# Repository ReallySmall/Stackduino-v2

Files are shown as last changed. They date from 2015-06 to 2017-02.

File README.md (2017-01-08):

Stackduino 2
==========
Please visit the project site for details: https://www.stackduino.net/boards/v2-2

Copyright 2017 Richard Iles

Permission is hereby granted, free of charge, to any person obtaining a copy of this software and associated documentation files (the "Software"), to deal in the Software without restriction, including without limitation the rights to use, copy, modify, merge, publish, distribute, sublicense, and/or sell copies of the Software, and to permit persons to whom the Software is furnished to do so, subject to the following conditions:

The above copyright notice and this permission notice shall be included in all copies or substantial portions of the Software.

THE SOFTWARE IS PROVIDED "AS IS", WITHOUT WARRANTY OF ANY KIND, EXPRESS OR IMPLIED, INCLUDING BUT NOT LIMITED TO THE WARRANTIES OF MERCHANTABILITY, FITNESS FOR A PARTICULAR PURPOSE AND NONINFRINGEMENT. IN NO EVENT SHALL THE AUTHORS OR COPYRIGHT HOLDERS BE LIABLE FOR ANY CLAIM, DAMAGES OR OTHER LIABILITY, WHETHER IN AN ACTION OF CONTRACT, TORT OR OTHERWISE, ARISING FROM, OUT OF OR IN CONNECTION WITH THE SOFTWARE OR THE USE OR OTHER DEALINGS IN THE SOFTWARE.

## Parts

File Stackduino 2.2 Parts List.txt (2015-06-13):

Partlist

Exported from Stackduino-SMD.sch at 13/06/2015 14:22:47

EAGLE Version 7.2.0 Copyright (c) 1988-2014 CadSoft

Assembly variant: 

Part          Value                   Device              Package            Library                  Sheet

A4988_CARRIER A4988BREAKOUT           A4988BREAKOUT       A4988BREAKOUT      RepRapjr                 1
ATMEGA328P    ATMEGA328P              ATMEGA328_SMT       TQFP32-08          SparkFun-DigitalIC       1
BATT_IN       JST-PH_3-PIN_HEADER     JST-PH_3-PIN_HEADER JST_B3B-PH_HEADER  SRG                      1
C1            22pF                    C                   C0805              eagle-ltspice            1
C2            0.1uF                   C                   C0805              eagle-ltspice            1
C3            0.1uF                   C                   C0805              eagle-ltspice            1
C4            10nF                    C                   C0805              eagle-ltspice            1
C5            0.1uF                   C                   C0805              eagle-ltspice            1
C6            22pF                    C                   C0805              eagle-ltspice            1
C7            0.1uF                   C                   C0805              eagle-ltspice            1
C8            100uF                   CAP_POLD            PANASONIC_D        SparkFun-Passives        1
C9            100uF                   CAP_POLD            PANASONIC_D        SparkFun-Passives        1
C10           100uF                   CAP_POLD            PANASONIC_D        SparkFun-Passives        1
C11           0.1uF                   C                   C0805              eagle-ltspice            1
C12           0.1uF                   C                   C0805              eagle-ltspice            1
C13           100nF                   C                   C0805              eagle-ltspice            1
C14           22uF                    C                   C0805              eagle-ltspice            1
C15           10nF                    C                   C0805              eagle-ltspice            1
D1            20v 1A                  MBRA140             SMA-DIODE          SparkFun-DiscreteSemi    1
D2            20v 1A                  MBRA140             SMA-DIODE          SparkFun-DiscreteSemi    1
DB15          DB15                    DB15                DB15               SparkFun-Connectors      1
DC_SOCKET     2.1MMJACKTHM            2.1MMJACKTHM        PJ-102A            adafruit                 1
FT232RL       FT232RLSSOP             FT232RLSSOP         SSOP28DB           SparkFun-DigitalIC       1
H1            MOUNT-PAD-ROUND2.8      MOUNT-PAD-ROUND2.8  2,8-PAD            holes                    1
H2            MOUNT-PAD-ROUND2.8      MOUNT-PAD-ROUND2.8  2,8-PAD            holes                    1
H3            MOUNT-PAD-ROUND2.8      MOUNT-PAD-ROUND2.8  2,8-PAD            holes                    1
H4            MOUNT-PAD-ROUND2.8      MOUNT-PAD-ROUND2.8  2,8-PAD            holes                    1
H_1           B4B-ZR                  B4B-ZR              B4B-ZR             jst-connectors           1
H_2           B4B-ZR                  B4B-ZR              B4B-ZR             jst-connectors           1
H_3           B3B-ZR                  B3B-ZR              B3B-ZR             jst-connectors           1
H_4           B5B-ZR                  B5B-ZR              B5B-ZR             jst-connectors           1
H_5           B10B-ZR                 B10B-ZR             B10B-ZR            jst-connectors           1
H_6           B2B-ZR                  B2B-ZR              B2B-ZR             jst-connectors           1
H_7           B2B-ZR                  B2B-ZR              B2B-ZR             jst-connectors           1
H_8           B2B-ZR                  B2B-ZR              B2B-ZR             jst-connectors           1
J1            JUMPER                  R                   R0805              eagle-ltspice            1
J2                                    PINHD-1X2           1X02               pinhead                  1
L1            33uH - Coilcraft DO3316 DO3316P             DO3316P            inductor-coilcraft       1
LM2675-3.3    LM2675M                 LM2675M             SO08               v-reg-3                  1
LTC2950       LTC2950CTS8-1TRPBF      LTC2950CTS8-1TRPBF  SOT65P280X100-8N   LTC_By_element14_Batch_1 1
LTC4412       LTC4412ES6PBF           LTC4412ES6PBF       SOT95P280X100-6N   LTC_By_element14_Batch_1 1
MCP23017      MCP23017SS              MCP23017SS          SSOP28             adafruit                 1
MICROSD       CON_MICROSDHINGED       CON_MICROSDHINGED   CON_MICROSD_HINGED dp_devices               1
MN1           BSS123                  BSS123              SOT23              transistor-small-signal  1
MP1           FDN306P                 FDN360P             SUPER-SOT3         transistor-power         1
MP2           FDN306P                 FDN360P             SUPER-SOT3         transistor-power         1
MP3           FDN340P                 FDN360P             SUPER-SOT3         transistor-power         1
OPT1          AVAGO HCPL-181-00BE     LTV816S             SMD4               optocoupler              1
OPT2          AVAGO HCPL-181-00BE     LTV816S             SMD4               optocoupler              1
QF1           8Mhz                    CRYSTALHC49U-V      HC49U-V            crystal                  1
R1            220 Ohm                 R                   R0805              eagle-ltspice            1
R2            220 Ohm                 R                   R0805              eagle-ltspice            1
R3            100K                    R                   R0805              eagle-ltspice            1
R4            2.7K                    R                   R0805              eagle-ltspice            1
R5            10K                     R                   R0805              eagle-ltspice            1
R6            4.7K                    R                   R0805              eagle-ltspice            1
R7            4.7K                    R                   R0805              eagle-ltspice            1
R8            10K                     R                   R0805              eagle-ltspice            1
R9            10K                     R                   R0805              eagle-ltspice            1
R10           10K                     R                   R0805              eagle-ltspice            1
R11           10K                     R                   R0805              eagle-ltspice            1
R12           100K                    R                   R0805              eagle-ltspice            1
R13           100K                    R                   R0805              eagle-ltspice            1
R14           100K                    R                   R0805              eagle-ltspice            1
R15           600K                    R                   R0805              eagle-ltspice            1
USB           USBSMD                  USBSMD              USB-MINIB          SparkFun-Connectors      1

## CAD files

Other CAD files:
Sketchup/Stackduino-2.2-Sketchup.skp

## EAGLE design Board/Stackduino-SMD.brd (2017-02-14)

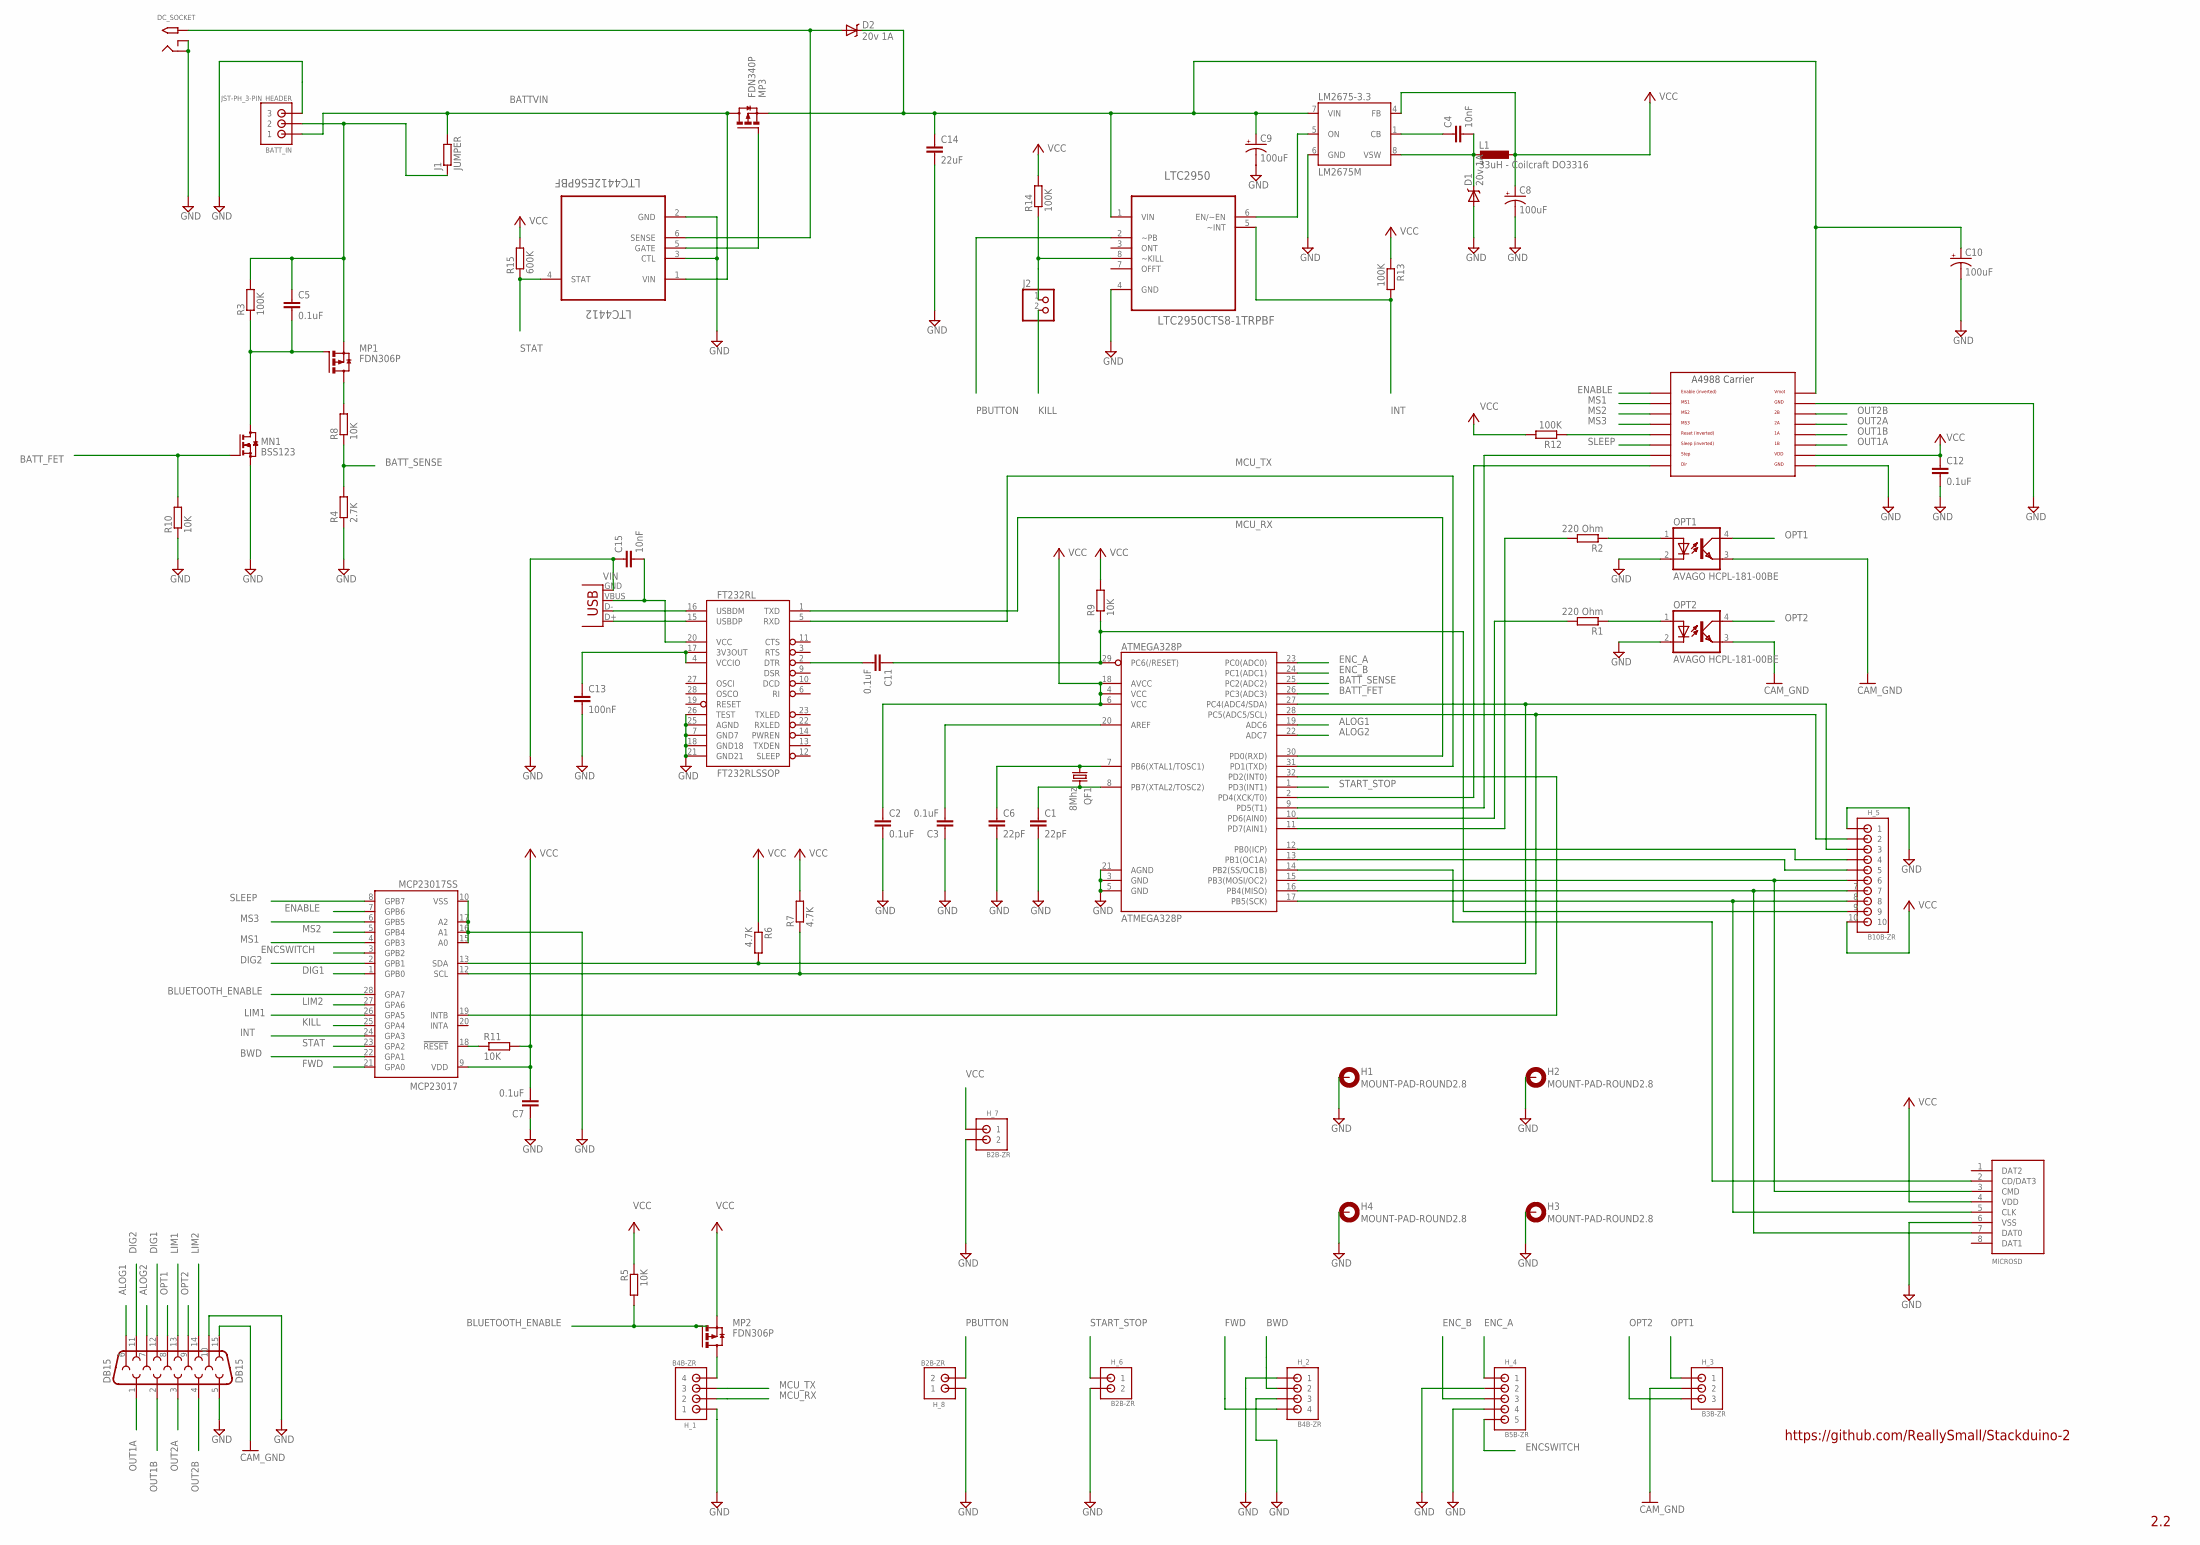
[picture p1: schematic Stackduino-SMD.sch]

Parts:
A4988_CARRIER: A4988BREAKOUT
ATMEGA328P: ATMEGA328P; TQFP32-08
BATT_IN: JST-PH_3-PIN_HEADER; JST_B3B-PH_HEADER
C1, C6: 22pF; C0805
C2, C3, C5, C7, C11, C12: 0.1uF; C0805
C4, C15: 10nF; C0805
C8, C9, C10: 100uF; PANASONIC_D
C13: 100nF; C0805
C14: 22uF; C0805
D1, D2: 20v 1A; SMA-DIODE
DB15: DB15
DC_SOCKET: 2.1MMJACKTHM; PJ-102A
FT232RL: FT232RLSSOP; SSOP28DB
H1, H2, H3, H4: MOUNT-PAD-ROUND2.8; 2,8-PAD
H_1, H_2: B4B-ZR
H_3: B3B-ZR
H_4: B5B-ZR
H_5: B10B-ZR
H_6, H_7, H_8: B2B-ZR
J1: JUMPER; R0805
J2: PINHD-1X2; 1X02
L1: 33uH - Coilcraft DO3316; DO3316P
LM2675-3.3: LM2675M; SO08
LTC2950: LTC2950CTS8-1TRPBF; SOT65P280X100-8N
LTC4412: LTC4412ES6PBF; SOT95P280X100-6N
MCP23017: MCP23017SS; SSOP28
MICROSD: CON_MICROSDHINGED; CON_MICROSD_HINGED
MN1: BSS123; SOT23
MP1, MP2: FDN306P; SUPER-SOT3
MP3: FDN340P; SUPER-SOT3
OPT1, OPT2: AVAGO HCPL-181-00BE; SMD4
QF1: 8Mhz; HC49U-V
R1, R2: 220 Ohm; R0805
R3, R12, R13, R14: 100K; R0805
R4: 2.7K; R0805
R5, R8, R9, R10, R11: 10K; R0805
R6, R7: 4.7K; R0805
R15: 600K; R0805
USB: USBSMD; USB-MINIB

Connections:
3V3_SET: C13.1, FT232RL.4 (VCCIO), FT232RL.17 (3V3OUT)
A4988_RESET: A4988_CARRIER.RST, R12.1
ALOG1: ATMEGA328P.19 (ADC6), DB15.6
ALOG2: ATMEGA328P.22 (ADC7), DB15.7
BATTVIN: BATT_IN.P1 (1), J1.2, LTC4412.1 (VIN), MP3.3 (D)
BATT_FET: ATMEGA328P.26 (PC3(ADC3)), MN1.1 (G), R10.2
BATT_SENSE: ATMEGA328P.25 (PC2(ADC2)), R4.2, R8.1
BATT_SENSE_UPSTREAM: MP1.3 (D), R8.2
BATT_VOLT: BATT_IN.P2 (2), C5.1, J1.1, MP1.2 (S), R3.2
BATT_VOLT_ENABLE: C5.2, MN1.3 (D), MP1.1 (G), R3.1
BLUETOOTH_ENABLE: MCP23017.28 (GPA7), MP2.1 (G), R5.2
BWD: H_2.2, MCP23017.22 (GPA1)
CAM_GND: DB15.15, H_3.2, OPT1.3 (EMIT), OPT2.3 (EMIT)
DIG1: DB15.12, MCP23017.1 (GPB0)
DIG2: DB15.11, MCP23017.2 (GPB1)
DIR: A4988_CARRIER.DIR, ATMEGA328P.2 (PD4(XCK/T0))
ENABLE: A4988_CARRIER.EN, MCP23017.7 (GPB6)
ENCSWITCH: H_4.5, MCP23017.3 (GPB2)
ENC_A: ATMEGA328P.23 (PC0(ADC0)), H_4.1
ENC_B: ATMEGA328P.24 (PC1(ADC1)), H_4.3
FWD: H_2.4, MCP23017.21 (GPA0)
GATE: LTC4412.5 (GATE), MP3.1 (G)
GND: A4988_CARRIER.GND, A4988_CARRIER.GND@0 (GND), ATMEGA328P.3 (GND), ATMEGA328P.5 (GND), ATMEGA328P.21 (AGND), BATT_IN.P3 (3), C1.2, C2.2, C3.1, C6.2, C7.1, C8.-, C9.-, C10.-, C12.2, C13.2, C14.2, C15.1, D1.A, DB15.5, DB15.10, DC_SOCKET.RING, DC_SOCKET.RING_SW, FT232RL.7 (GND7), FT232RL.18 (GND18), FT232RL.21 (GND21), FT232RL.25 (AGND), FT232RL.26 (TEST), H1.B2,8, H2.B2,8, H3.B2,8, H4.B2,8, H_1.1, H_2.1, H_2.3, H_4.2, H_4.4, H_5.1, H_6.2, H_7.2, H_8.1, LM2675-3.3.6 (GND), LTC2950.4 (GND), LTC4412.2 (GND), LTC4412.3 (CTL), MCP23017.10 (VSS), MCP23017.15 (A0), MCP23017.16 (A1), MCP23017.17 (A2), MICROSD.6 (VSS), MN1.2 (S), OPT1.2 (C), OPT2.2 (C), R4.1, R10.1, USB.GND
I2C_SCL: ATMEGA328P.28 (PC5(ADC5/SCL)), H_5.2, MCP23017.12 (SCL), R7.1
I2C_SDA: ATMEGA328P.27 (PC4(ADC4/SDA)), H_5.3, MCP23017.13 (SDA), R6.2
INT: LTC2950.5 (~INT), MCP23017.24 (GPA3), R13.2
KILL: J2.2, MCP23017.25 (GPA4)
KILL_2: J2.1, LTC2950.8 (~KILL), R14.1
LIM1: DB15.13, MCP23017.26 (GPA5)
LIM2: DB15.14, MCP23017.27 (GPA6)
LM2675_CB: C4.1, LM2675-3.3.1 (CB)
LM2675_ENABLE: LM2675-3.3.5 (ON), LTC2950.6 (EN/~EN)
LM2675_OUT: C4.2, D1.C, L1.1, LM2675-3.3.8 (VSW)
MCP_INT: ATMEGA328P.32 (PD2(INT0)), MCP23017.19 (INTB)
MCP_RESET: MCP23017.18 (!RESET), R11.1
MCU_RX: ATMEGA328P.30 (PD0(RXD)), FT232RL.1 (TXD), H_1.2
MCU_TX: ATMEGA328P.31 (PD1(TXD)), FT232RL.5 (RXD), H_1.3
MISO: ATMEGA328P.16 (PB4(MISO)), H_5.7, MICROSD.7 (DAT0)
MOSI: ATMEGA328P.15 (PB3(MOSI/OC2)), H_5.6, MICROSD.3 (CMD)
MS1: A4988_CARRIER.MS1, MCP23017.4 (GPB3)
MS2: A4988_CARRIER.MS2, MCP23017.5 (GPB4)
MS3: A4988_CARRIER.MS3, MCP23017.6 (GPB5)
unnamed: C11.2, FT232RL.2 (DTR)
unnamed: FT232RL.16 (USBDM), USB.D-
unnamed: FT232RL.15 (USBDP), USB.D+
unnamed: ATMEGA328P.20 (AREF), C3.2
unnamed: H_1.4, MP2.3 (D)
unnamed: C15.2, FT232RL.20 (VCC), USB.VBUS
OPT1: DB15.8, H_3.1, OPT1.4 (COL)
OPT1_IN: OPT1.1 (A), R2.1
OPT1_MCU: ATMEGA328P.11 (PD7(AIN1)), R2.2
OPT2: DB15.9, H_3.3, OPT2.4 (COL)
OPT2_IN: OPT2.1 (A), R1.1
OPT2_MCU: ATMEGA328P.10 (PD6(AIN0)), R1.2
OUT1A: A4988_CARRIER.1B, DB15.1
OUT1B: A4988_CARRIER.1A, DB15.2
OUT2A: A4988_CARRIER.2A, DB15.3
OUT2B: A4988_CARRIER.2B, DB15.4
PBUTTON: H_8.2, LTC2950.2 (~PB)
RESET: ATMEGA328P.29 (PC6(/RESET)), C11.1, H_5.9, R9.1
SCK: ATMEGA328P.17 (PB5(SCK)), H_5.8, MICROSD.5 (CLK)
SLEEP: A4988_CARRIER.SLP (SLEEP), MCP23017.8 (GPB7)
SS_1: ATMEGA328P.14 (PB2(SS/OC1B)), MICROSD.2 (CD/DAT3)
SS_2: ATMEGA328P.13 (PB1(OC1A)), H_5.5
SS_3: ATMEGA328P.12 (PB0(ICP)), H_5.4
START_STOP: ATMEGA328P.1 (PD3(INT1)), H_6.1
STAT: LTC4412.4 (STAT), MCP23017.23 (GPA2), R15.1
STEP: A4988_CARRIER.STEP, ATMEGA328P.9 (PD5(T1))
V+: A4988_CARRIER.VMOT, C9.+, C10.+, C14.1, D2.C, LM2675-3.3.7 (VIN), LTC2950.1 (VIN), MP3.2 (S)
VCC: A4988_CARRIER.VDD, ATMEGA328P.4 (VCC), ATMEGA328P.6 (VCC), ATMEGA328P.18 (AVCC), C2.1, C7.2, C8.+, C12.1, H_5.10, H_7.1, L1.2, LM2675-3.3.4 (FB), MCP23017.9 (VDD), MICROSD.4 (VDD), MP2.2 (S), R5.1, R6.1, R7.2, R9.2, R11.2, R12.2, R13.1, R14.2, R15.2
VIN: D2.A, DC_SOCKET.TIP, LTC4412.6 (SENSE)
XTAL1: ATMEGA328P.7 (PB6(XTAL1/TOSC1)), C6.1, QF1.1
XTAL2: ATMEGA328P.8 (PB7(XTAL2/TOSC2)), C1.1, QF1.2

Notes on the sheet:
https://github.com/ReallySmall/Stackduino-2
2.2

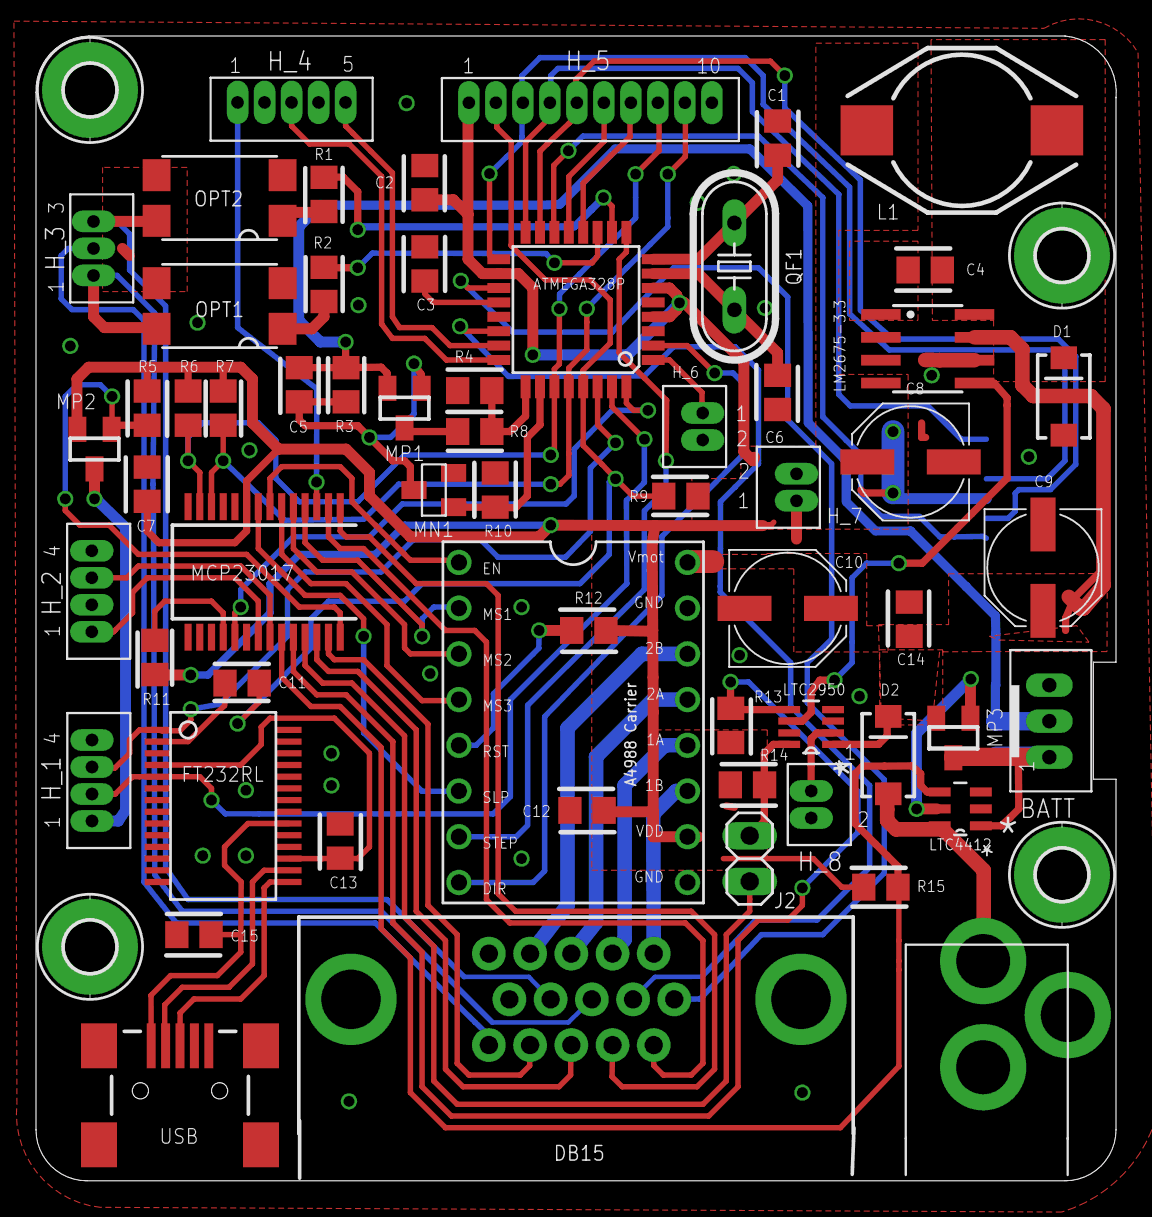
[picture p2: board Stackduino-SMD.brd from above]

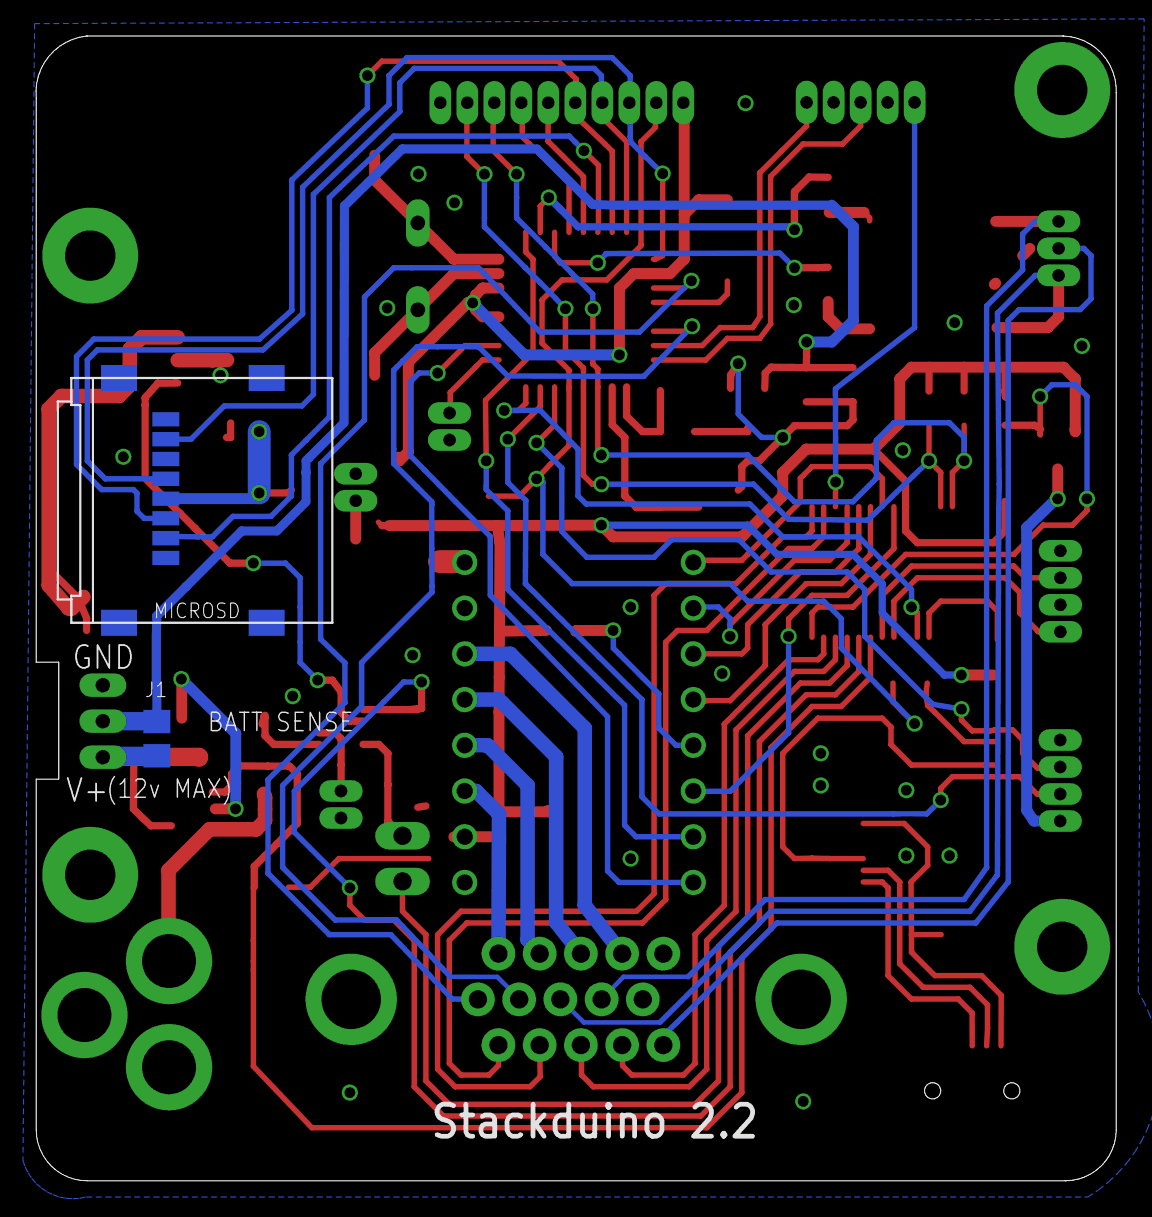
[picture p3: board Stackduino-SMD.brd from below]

Board: 2 copper layers, 60.0 x 63.6 mm, 66 parts (2 on the bottom side), 73 nets.

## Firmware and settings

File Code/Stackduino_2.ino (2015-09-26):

//////////////////////////////////////////////////////////////////////////////////////////////////////////
//  STACKDUINO 2 (BETA)                                                                                 //
//                                                                                                      //
//  https://github.com/ReallySmall/Stackduino-2                                                         //
//                                                                                                      //
//  An Arduino compatible Focus Stacking Controller optimised for mobile use                            //
//  Richard Iles 2014                                                                                   //
//                                                                                                      //
//  Written for use with the Digole 128 x 64 OLED module using default font (4 rows of 16 chars)        //
//  To support other fonts or screens, some recoding will be required                                   //
////////////////////////////////////////////////////////////////////////////////////////////////////////*/



/* DEFINES AND DEPENDENCIES */
#define _Digole_Serial_I2C_ // OLED screen configured with solder jumper to run in I2C mode
#define OLED_ROWS 4 // OLED text rows
#define OLED_COLS 16 // OLED text columns
#define ENC_A A0 // Rotary encoder
#define ENC_B A1 // Rotary encoder
#define ENC_PORT PINC // Rotary encoder
#define settings_elements 4 // Number of properties in each settings

#include "DigoleSerial.h" // https://github.com/chouckz/HVACX10Arduino/blob/master/1.0.1_libraries/DigoleSerial/DigoleSerial.h
#include "Wire.h" //
#include "Adafruit_MCP23017.h" //
#include "SPI.h"
#include "SD.h"
#include "avr/pgmspace.h"



/* CREATE REQUIRED OBJECTS */
Adafruit_MCP23017 mcp; // 16 pin IO port expander
DigoleSerialDisp screen(&Wire, '\x27'); // Digole OLED in i2c mode

typedef struct { // A struct type for storing char arrays
  char title [OLED_COLS + 1];
} stringConstants;

const stringConstants settings_titles[] PROGMEM = { // A struct of char arrays stored in Flash
  {"Stackduino v2.2"},
  {"Slice size"},
  {"Slices"},
  {"Pause for"},
  {"Mirror lockup"},
  {"Bracketing"},
  {"Return to home"},
  {"Units"},
  {"Motor speed"},
  {"Microsteps"},
  {"Bluetooth"}
};

char uom_chars[3] = {'u', 'm', 'c'};

struct Settings { // A struct type for storing settings

  int value; // The setting value
  byte lower; // The lowest value the setting may have
  int upper; // The highest value the setting may have
  byte multiplier; // Any multiplier to apply when the setting is incremented

} settings[] = { // A struct of user menu settings
  {}, // The home screen - not actually used by any functions at the moment, but the placeholder array must exist to maintain the correct indexing
  {10, 10, 500, 1}, // "Slice size"
  {10, 10, 500, 10}, // "Number of slices"
  {5, 1, 60, 1}, // "Pause time"
  {0, 0, 1, 1}, // "Mirror lockup"
  {1, 1, 10, 1}, // "Bracketing"
  {0, 0, 1, 1}, // "Return to start"
  {0, 0, 2, 1}, // "Unit of measure"
  {2, 1, 8, 1}, // "Stepper speed"
  {4, 0, 4, 1}, // "Microstepping"
  {0, 0, 1, 1} // "Bluetooth"
};

byte settings_count = sizeof(settings) / sizeof(Settings); // The number of settings
char char_buffer[OLED_COLS + 1]; // make sure this is large enough for the largest string it must hold



/* SET UP REMAINING ATMEGA PINS */
const byte mcp_int = 2; // Incoming MCP23017 interrupts
const byte btn_main = 3;  // Main start/ stop stack button
const byte step_dir = 4; // Direction pin on A4988 stepper driver
const byte do_step = 5; // Step pin on A4988 stepper driver
const byte cam_focus = 6; // Camera autofocus signal
const byte cam_shutter = 7; // Camera shutter signal
const byte sd_ss = 10; // SPI slave select for SD card slot
const byte batt_sense = A2; // Battery voltage sampling
const byte batt_fet = 17; // Connect/ disconnect battery voltage sampling line
const byte alog_1 = A6; // Analogue pin (supports analogueRead() only) broken out through DB15 - currently unused
const byte alog_2 = A7; // Analogue pin (supports analogueRead() only) broken out through DB15 - currently unused



/*  SET UP MCP23017 PINS */
const byte step_bwd = 0; // For manual stage positioning
const byte step_fwd = 1; // For manual stage positioning
const byte pwr_stat = 2; // LTC4412 stat pin - indicates whether controller is currently powered by wall adapter or battery
const byte switch_off_flag = 3; // LTC2950 int pin - signals to the controller that it is about to be switched off
const byte switch_off = 4; // LTC2950 kill pin - disables 3.3v regulator and switches off controller
const byte limit_switch_front = 5; // Limit switch to stop stepper motor if end of travel is reached
const byte limit_switch_back = 6; // Limit switch to stop stepper motor if end of travel is reached
const byte bluetooth_pwr_toggle = 7; // Toggles power to bluetooth breakout board header
const byte connected_hardware = 8; // Digital pin broken out through DB15 - currently unused
const byte dig_1 = 9;// Digital pin broken out through DB15 - currently unused
const byte btn_rotary = 10; // Select/ unselect menu item button
const byte ms1 = 11; // Toggles A4988 stepper driver MS1 pin to control degree of microstepping
const byte ms2 = 12; // Toggles A4988 stepper driver MS2 pin to control degree of microstepping
const byte ms3 = 13; // Toggles A4988 stepper driver MS3 pin to control degree of microstepping
const byte step_enable = 14; // Disable/enables A4988 stepper driver to conserve power
const byte step_sleep = 15; // Sleep/wake A4988 stepper driver to conserve power



/* SETTINGS */
const int uom_multipliers[] = {1, 1000, 10000}; // Multipliers for active unit of measure (mn, mm or cm)
const byte micro_stepping[2][5][3] = {{{1},       {2},       {4},       {8},       {16}}, // Degrees of microstepping the A4988 stepper driver can use
  {{0, 0, 0}, {1, 0, 0}, {0, 1, 0}, {1, 1, 0}, {1, 1, 1}}
}; // HIGH/ LOW combinations to set A4988 MSx pins at

float active_hardware_calibration_setting;

volatile boolean start_stack = false; // False when in the menu, true when stacking
volatile boolean traverse_menus = true; // True when scrolling through menus, false when changing a menu item's value
volatile boolean mcp_int_fired = false; // True whenever a pin on the mcp23017 with a listener went low
volatile byte btn_reading; // The current reading from the button
volatile byte btn_previous = LOW; // The previous reading from the button
volatile long btn_time = 0; // The last time the button was toggled

boolean app_connected = false; // Whether a remote application is actively communicating with the controller
boolean can_disable_stepper = true; // Whether to disable the A4988 stepper driver when possible to save power and heat
boolean idle = true; // True until the controller is interacted with
boolean update_display = true; // True whenever functions are called which change a setting's value
boolean update_header = true; // True whenever the value of an item in the header changes
boolean home_screen = true;
boolean previous_direction;

float calc_volts = 0.00; // The actual battery voltage as calculated through the divider

int menu_item = 0; // The active menu item
int increments = 0; // Count increments the active menu setting should be changed by on the next poll
byte sys_off = 20; // Minutes of inactivity to wait until controller switches itself off - set to 0 to disable
byte slice_count = 0; // Count of number of focus slices made so far in the stack

unsigned long time_stack_started;

char* app_conn_icon = "";

File settings_file;



/* SETUP() */
void setup() {

  /* SET ATMEGA PINMODES AND PULLUPS */
  pinMode(mcp_int, INPUT); digitalWrite(mcp_int, HIGH);
  pinMode(btn_main, INPUT); digitalWrite(btn_main, HIGH);
  pinMode(ENC_A, INPUT); digitalWrite(ENC_A, HIGH);
  pinMode(ENC_B, INPUT); digitalWrite(ENC_B, HIGH);
  pinMode(step_dir, OUTPUT); digitalWrite(step_dir, LOW);
  pinMode(do_step, OUTPUT); digitalWrite(do_step, LOW);
  pinMode(cam_focus, OUTPUT); digitalWrite(cam_focus, LOW);
  pinMode(cam_shutter, OUTPUT); digitalWrite(cam_shutter, LOW);
  pinMode(batt_fet, OUTPUT); digitalWrite(batt_fet, LOW);
  pinMode(sd_ss, OUTPUT);

  /* START MCP23017 AND SET PINMODES AND PULLUPS */
  mcp.begin(); // Using default address 0

  mcp.pinMode(step_bwd, INPUT); mcp.pullUp(step_bwd, HIGH);
  mcp.pinMode(step_fwd, INPUT); mcp.pullUp(step_fwd, HIGH);
  mcp.pinMode(pwr_stat, INPUT); mcp.pullUp(pwr_stat, LOW);
  mcp.pinMode(switch_off_flag, INPUT);
  mcp.pinMode(switch_off, OUTPUT); mcp.digitalWrite(switch_off, HIGH);
  mcp.pinMode(limit_switch_front, INPUT); mcp.pullUp(limit_switch_front, HIGH);
  mcp.pinMode(limit_switch_back, INPUT); mcp.pullUp(limit_switch_back, HIGH);
  mcp.pinMode(bluetooth_pwr_toggle, OUTPUT); mcp.digitalWrite(bluetooth_pwr_toggle, HIGH);
  mcp.pinMode(connected_hardware, INPUT); mcp.pullUp(connected_hardware, HIGH);
  mcp.pinMode(dig_1, INPUT); mcp.pullUp(dig_1, HIGH);
  mcp.pinMode(btn_rotary, INPUT); mcp.pullUp(btn_rotary, HIGH);
  mcp.pinMode(ms1, OUTPUT); mcp.digitalWrite(ms1, HIGH);
  mcp.pinMode(ms2, OUTPUT); mcp.digitalWrite(ms2, HIGH);
  mcp.pinMode(ms3, OUTPUT); mcp.digitalWrite(ms2, HIGH);
  mcp.pinMode(step_enable, OUTPUT);
  mcp.pinMode(step_sleep, OUTPUT); mcp.digitalWrite(step_sleep, HIGH);

  /* SET UP INTERRUPTS */
  attachInterrupt(0, mcpInterrupt, FALLING); // ATMega external interrupt 0
  attachInterrupt(1, cancelStack, FALLING); // ATMega external interrupt 1

  pciSetup(ENC_A); // ATMega pin change interrupt
  pciSetup(ENC_B); // ATMega pin change interrupt

  mcp.setupInterrupts(true, false, LOW); // MCP23017 interupts (trigger ATMega external interrupt 0)
  mcp.setupInterruptPin(switch_off_flag, FALLING);
  mcp.setupInterruptPin(pwr_stat, CHANGE); //Need to catch both changes from LOW to HIGH and HIGH to LOW

  /* FINAL PRE-START CHECKS AND SETUP */
  Serial.begin(9600); // Start serial (always initialise at 9600 for compatibility with OLED)
  getHardware(); // Get the type of the attached stacker
  battMonitor(); // Check the battery level
  loadSettings(); // Attempt to load settings from SD card  
}



/*////////////////////////////////////////////////////////////////////////////////////////////////////////
// FUNCTIONS                                                                                            //
////////////////////////////////////////////////////////////////////////////////////////////////////////*/



/* UPDATE THE SCREEN WHEN DATA CHANGES
*
* Clears the screen then re-outputs it
*
*/
void screenUpdate() { /* WIPE THE SCREEN, PRINT THE HEADER AND SET THE CURSOR POSITION */

  screen.clearScreen(); // Repaints the screen blank
  screenPrintBluetooth(); // Display an icon for current bluetooth connection state
  screenPrintPowerSource(); // Display the current power source in top right corner

  screen.drawBox(1, 17, 128, 1); // Draw a horizontal line to mark out the header section
  screen.setPrintPos(0, 2); // Set text position to beginning of content area
  idle = false; // Flag that the system was recently used

}



/* PRINT TEXT ON DIGOLE OLED SCREEN
*
* Assumes the default font is in use (allowing 4 rows of 16 characters)
*
* char_length => The length of the string in the char buffer
* text => The string to be centered and printed
* print_pos_y => The text line to print on
*
*/
void screenPrint(byte char_length, char* text, byte print_pos_y = 4) {

  // Calculate the start point on x axis for the number of characters in the string to print it centrally
  byte print_pos_x = (OLED_COLS - char_length) / 2;
  
  screen.setPrintPos(print_pos_x, print_pos_y); // Set the start point for printing
  
  byte offset_x = char_length % 2 != 0 ? 4 : 0; // If the string to print is an odd number in length, apply an offset to centralise it
  byte offset_y = print_pos_y == 4 ? -2 : 0; // If printing on line 4, nudge upwards a bit to prevent lower parts of characters like 'g' being cut off

  screen.setTextPosOffset(offset_x, offset_y); // Set the required positioning offsets defined above
  
  screen.print(text); // Finally, print the centered text to the screen
  
}



/* SET HARDWARE CONSTANT
*
* Detect the stacking hardware connected to and set constant
* The controller relies on the assumption that 1 full step made by the stepper motor will move the
* linear stage by 1 (or as close as possible to 1) micron.
* To achieve this relationship, the number of step signals generated should be multiplied by a constant
* (obtained through a little maths and experimentation) which is unique to your hardware.
*
*/
void getHardware() {
  if (mcp.digitalRead(connected_hardware) == HIGH) {
    active_hardware_calibration_setting = 1;
  } else {
    active_hardware_calibration_setting = 1.5; // TODO: This is a random example number, work out the actual one
  }
}



/* LOAD AND SAVE SETTINGS
*
* load settings from SD card/ save settings to SD card
*
*/
void loadSettings() {
  
  // If a connection to the SD card couldn't be established
  if (!SD.begin(sd_ss)) {
    screenUpdate();
    screenPrint(sprintf_P(char_buffer, PSTR("SD error")), char_buffer, 4);
    delay(1000);
    return;
  }

  // Otherwise attempt to get the settings string from the SD card
  settings_file = SD.exists("tmpdata.txt") ? SD.open("tmpdata.txt", FILE_READ) : SD.open("settings.txt", FILE_READ);
  
  // If there was an issue attempting to open the file
  if (!settings_file) {

    screenPrint(sprintf_P(char_buffer, PSTR("SD file error")), char_buffer, 4);
    delay(1000);
    screenPrint(sprintf_P(char_buffer, PSTR("Using defaults")), char_buffer, 4);
    delay(1000);
    
  // Otherwise start copying the settings from the file into memory  
  } else {
    
    byte setting_index = 0; // Which menu setting to populate
    byte property_index = 0; // Index of the menu setting property to populate next
    byte char_buffer_index = 0; // Index of the char buffer to add next character from the sd read buffer
    char file_character; // The character currently in the sd read buffer
    boolean record_chars = false; // Whether to copy or ignore incoming characters

    while (settings_file.available()) { // Until the end of the file is reached, read it one character at a time

      file_character = settings_file.read(); // Current character in the file

      // Don't bother trying to process anything on the settings line until reaching an '{' 
      // The preceeding content is to make the file human readable and not used by the controller
      if (record_chars) { // If in a section of the file containing settings data

        // Example of a settings line from file:
        //
        // Slice size = {15,10,250,1};
        //
        // A ',' marks the end of a setting property and a '}' marks the end of the parent setting
        // If the current character is neither of these then it's part of, or the whole of a setting property and should be processed
        if (file_character != ',' && file_character != '}') {
          char_buffer[char_buffer_index] = file_character; // Add character to char buffer
          char_buffer_index++; // Advance to next index of char buffer to store any subsequent character for this setting property
          char_buffer[char_buffer_index] = '\0'; // Null terminate the string 
        }
        //settings_file.readBytesUntil(',' || '}', char_buffer, 4);


        // When all the characters for the current setting property have been captured, copy the char buffer contents to the settings struct in memory
        if (file_character == ',' || file_character == '}') {
          switch (property_index) { // The index of the current setting property
            case 0: // Setting value
              settings[setting_index].value = atoi(char_buffer);
              break;
            case 1: // Setting value lower limit
              settings[setting_index].lower = atoi(char_buffer);
              break;
            case 2: // Setting value upper limit
              settings[setting_index].upper = atoi(char_buffer);
              break;
            case 3: // Any multiplier that functions should apply to the setting value
              settings[setting_index].multiplier = atoi(char_buffer);
              break;
          }

          memset(char_buffer, 0, sizeof(char_buffer)); // Clear the char buffer for the next property
          char_buffer_index = 0; // Reset the char buffer indexer
          property_index++; // Move to the next property of the current setting

          // Once all properties of a setting have been copied
          if (file_character == '}') { 
            record_chars = false; // Stop recording from the sd read buffer
            property_index = 0; // Reset the setting property indexer
            setting_index++; // And move to the next setting
          }

        }
      }
      // Start recording from the next recieved character onwards
      if(file_character == '{'){
        record_chars = true;
      }
    }
    
    settings_file.close(); // Close the file once it has been read
    SD.remove("tmpdata.txt"); // Delete the temporary settings file if it exists  
    
  }

}



void saveSettings(boolean sleep = false) {

  //Open and empty the settings file if it exists, otherwise create it
  settings_file = sleep == true ? SD.open("tmpdata.txt", O_WRITE | O_CREAT | O_TRUNC) : SD.open("settings.txt", O_WRITE | O_CREAT | O_TRUNC);
  
  screenUpdate();
  screenPrint(sprintf_P(char_buffer, PSTR("Saving settings")), char_buffer, 2);

  // Loop through settings in memory and write back to the file
  for (byte i = 0; i < settings_count; i++) {
    
    stringConstants thisSettingTitle; //Retrieve the setting title from progmem
    memcpy_P (&thisSettingTitle, &settings_titles[i], sizeof thisSettingTitle);
    settings_file.write(thisSettingTitle.title);    
    settings_file.write(" = {");
    settings_file.write(settings[i].value);
    settings_file.write(",");
    settings_file.write(settings[i].lower);
    settings_file.write(",");
    settings_file.write(settings[i].upper);
    settings_file.write(",");
    settings_file.write(settings[i].multiplier);
    settings_file.write("};");
    settings_file.println();
        
  }

  settings_file.close(); // Save the file

}



/* POWER OFF
*
* The controller powers itself off by pulling the enable pin on the voltage regulator low
*
*/
void sysOff() {

  screenUpdate();
  screenPrint(sprintf_P(char_buffer, PSTR("System off")), char_buffer, 2);
  delay(1000);
  mcp.digitalWrite(switch_off, LOW);

}
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
void loop() {



  /* MENUS AND STAGE CONTROL
  *
  * Manual control of linear stage is only enabled when in this section of the loop
  * - prevents running stacks being ruined by accidental button presses
  *
  * Menu navigation controlled either by rotary encoder with integral push button, or via serial
  *
  */
  if (!start_stack) { // User settings menus and manual stage control

    if (mcp_int_fired) handleMcpInterrupt(); // Catch interrupts and run any required functions
    btnPress(3);
    btnPress(10);
    btnPress(0);
    btnPress(1);
    serialCommunications();  // Check for commands via serial
    menuInteractions(); // Change menu options and update the screen when changed
    sysTasks(); // Run timer driven tasks such as battery level checks and auto switch off

  }



  /* FOCUS STACK
  *
  * Images are captured, the stage is advanced and the process is repeated for as many times as needed
  *
  */
  else {

    byte slice_size = settings[1].value;
    byte slices = settings[2].value;
    
    time_stack_started = millis();

    slice_count = 1; // Register the first image(s) of the stack is being taken
    screenPrintPositionInStack(); // Print the current position in the stack
    captureImages(); // Take the image(s) for the first slice of the stack

    for (unsigned int i = 1; i < slices; i++) { // For each subsequent focus slice in the stack

      slice_count++; // Record slices made in the stack so far

      if (stackCancelled()) break; // Exit early if the stack has been cancelled

      screenPrintPositionInStack(); // Print the current position in the stack
      // Print that the stage is being advanced by x units
      screenPrint(sprintf_P(char_buffer, PSTR("Advance %d%c%c"), slice_size, uom_chars[settings[7].value], uom_chars[1]), char_buffer, 4);

      if (stackCancelled()) break; // Exit early if the stack has been cancelled

      stepperDriverEnable(true, 1); // Enable the stepper driver and set the direction to forwards
      stepperMoveOneSlice(1); // Move forward by one focus slice

      if (!stepperDriverInBounds()) stepperDriverClearLimitSwitch(); // Clear hit limit switch
      if (stackCancelled()) break; // Exit early if the stack has been cancelled

      stepperDriverEnable(false); // Disable the stepper driver
      captureImages(); // Take image(s)

    }

    stackEnd(); // End of focus stack tasks

  }
}

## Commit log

2013-12-07 FT232RL circuit added
    [stackduino-2-smd.fzz]
2013-12-08 Various additions
    [stackduino-2-smd.fzz]
2013-12-08 Completed draft breadboard layout
    [stackduino-2-smd.fzz]
2014-01-19 Initial commit of eagle files
    [Stackduino-SMD.brd, Stackduino-SMD.sch]
2014-01-20 Latest progress on schematic
2014-01-22 Added a3967 wiring
    [Stackduino-SMD.sch]
2014-01-24 Latest progress
    [Stackduino-SMD.brd]
2014-01-31 Initial layout of board
    [Stackduino-SMD.brd, Stackduino-SMD.sch]
2014-02-17 Substituted in a4988 polulu driver
    [Stackduino-SMD.brd, Stackduino-SMD.sch]
2014-03-30 Fixed tx/rx and test pin errors
    [Stackduino-SMD.brd, Stackduino-SMD.sch]
2014-03-31 Copied in Stackduino 1 sketch to adapt
    [Stackduino-SMD.brd, Stackduino-SMD.sch]
2014-04-08 added further mcp interrupt functions
2014-04-12 Amended cap values on crystal
    [Stackduino-SMD.brd, Stackduino-SMD.sch]
2014-04-12 added power source sensing on startup
2014-04-14 Added countdown on camera pause
2014-04-16 reconfigured encoder listening
2014-04-17 fixed hang on interrupt
    [Stackduino_2.ino]
2014-05-28 changes inc battery monitor
    [Stackduino-SMD.brd, Stackduino-SMD.sch]
2014-06-01 Battery monitor and VMOT Mosfets added
    [Stackduino-SMD.brd, Stackduino-SMD.sch]
2014-06-04 reorganised traces to avoid inductor
    [Stackduino-SMD.brd, Stackduino-SMD.sch]
2014-06-05 Changed inductor placement
    [Stackduino-SMD.brd]
2014-06-06 added camera input
    [Stackduino-SMD.brd, Stackduino-SMD.sch]
2014-06-08 Beginning to re-layout traces on grid
    [Stackduino-SMD.brd, Stackduino-SMD.sch]
2014-06-18 latest progress on brd v2.1
    [Stackduino-SMD.brd, Stackduino-SMD.sch]
2014-06-29 topside board nearly complete
    [Stackduino-SMD.brd, Stackduino-SMD.sch]
2014-07-12 nearly there,,,
    [Stackduino-SMD.brd, Stackduino-SMD.sch]
2014-07-17 no errors in DRC!
    [Stackduino-SMD.brd]
2014-07-20 Ready for checking
    [Stackduino-SMD.brd, Stackduino-SMD.sch]
2014-07-21 Cleared ERC warnings
    [Stackduino-SMD.brd, Stackduino-SMD.sch]
2014-08-02 switching to 3.3v, reworked mosfets
    [Stackduino-SMD.brd, Stackduino-SMD.sch]
2014-08-08 silkscreen outlines to 0805 caps and resistors
    [Stackduino-SMD.brd, Stackduino-SMD.sch]
2014-08-30 Slight change to jst footprint plus solder stencil
    [Stackduino-SMD.brd, Stackduino-SMD.sch, Stackduino_SMD_2.1_Stencil.dxf]
2014-09-19 initial code for battery monitoring and bluetooth
    [Stackduino-SMD.brd, Stackduino-SMD.sch]
2014-10-17 Battery monitor working and calibrated
2014-10-25 Trying to get mcp23017 interrupts working
2014-11-02 fwd manual control fixed and non-blocking delays
    [Stackduino_2.ino]
2014-11-20 Tinkering with pin change interrupts
2014-11-23 rotary encoder interrupts testing
2014-12-05 Replaced uses of String with char arrays
    [Stackduino_2.ino]
2015-02-26 Updated parts list for v2.2
    and removed out of date infor for v2.1
    Please enter the commit message for your changes. Lines starting
    [Stackduino_SMD_2.1_Stencil.dxf]
2015-03-07 added sketchup model for enclosure planning
    [Stackduino-2.2-Sketchup.skp]
2015-04-19 Fixed load settings from SD
    [Stackduino-2.2-Sketchup.skp]
2015-05-01 Fixed load function error
    [Stackduino_2.ino]
2015-05-03 Automatic centred printing
2015-05-08 short and long press manual control
    [Stackduino_2.ino]
2015-05-10 reverted to old pause countdown method
    [Stackduino_2.ino]
2015-05-15 fixed pwr_stat interrupt
2015-05-25 consolidated button debouncing
2015-06-13 fixed incorrect reistor value
    [Stackduino-2.2-Sketchup.skp]
2015-09-26 File tidyup
    [Stackduino-2.2-Sketchup.skp]
2017-02-14 Added Eagle files for board
    [Stackduino-SMD.brd, Stackduino-SMD.sch]

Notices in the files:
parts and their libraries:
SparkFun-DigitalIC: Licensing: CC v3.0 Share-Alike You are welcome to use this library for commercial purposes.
